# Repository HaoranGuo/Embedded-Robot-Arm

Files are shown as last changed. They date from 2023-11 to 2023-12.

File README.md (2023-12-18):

# Embedded Robot Arm
This repository is aimed for Comprehensive Training on Measurement and Control of Mechatronics Course Project at HUST.

## Overview
> In this project, the unit of length is **mm**

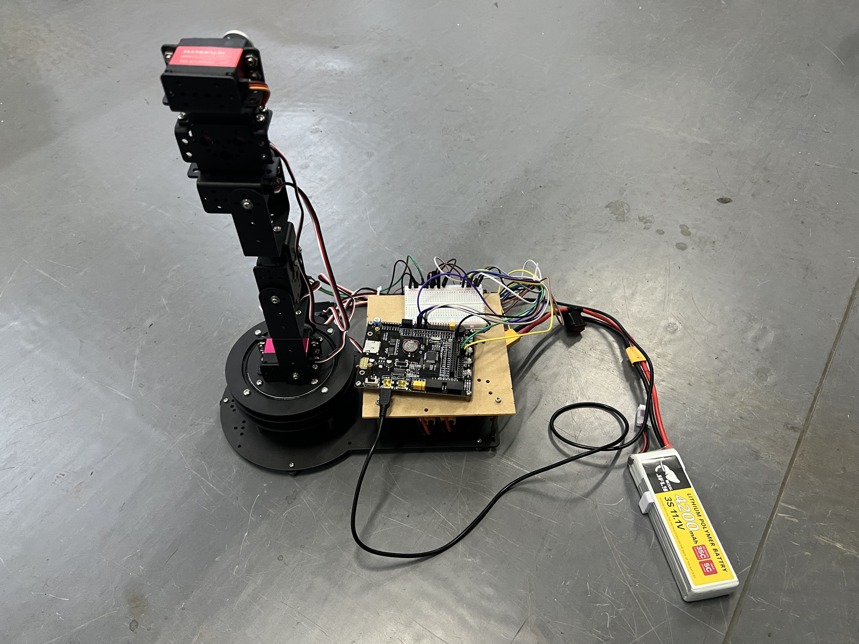
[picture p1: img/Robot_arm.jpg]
robot


In this course, we were required to start with some projects that are consist of mechanics, electrical circuits, and control systems. As a result, I decided to develop a cost-effective six-axis robotic arm.

We first refer to the key size of Universal Robot UR3. We tried to resize the robotic arm to a smaller size.

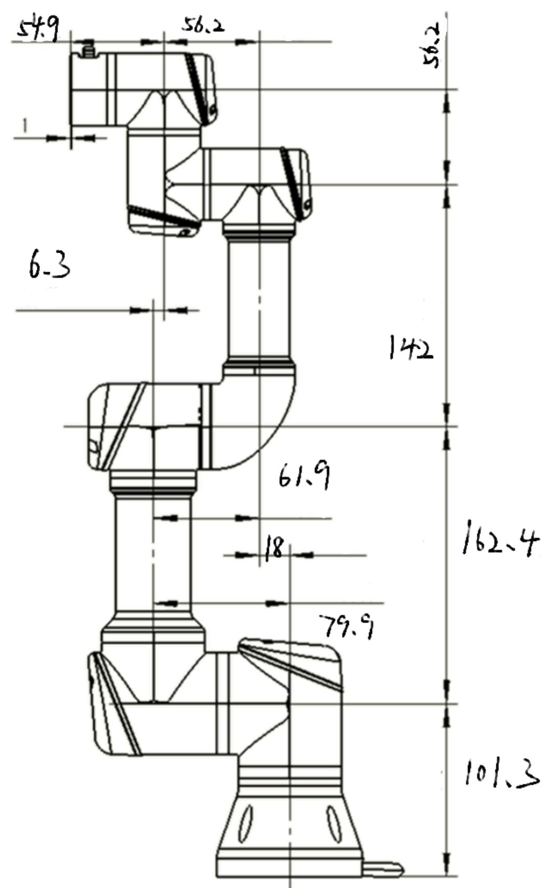
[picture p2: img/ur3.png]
ur3


This robotic arm contains six rotatable joints, allowing it to move as flexibly as possible within the workspace. The DH parameters of the robotic arm are as follows:

**Standard DH:**
| $i$ | $d_i$ | $a_i$ | $\alpha_i$ | $\theta_i$ |
| :--- | :---: | :---: | :---: | :---: |
| 1 | 0 | -9.55 | $\pi\over2$ | $\theta_1$ |
| 2 | 0 | -104 | 0 | $\theta_2$ |
| 3 | 0 | -96.4 | 0 | $\theta_3$ |
| 4 | 0 | 0 | $\pi\over2$ | $\theta_4$ |
| 5 | 80.66 | 0 | $-{{\pi}\over{2}}$ | $\theta_5$ |
| 6 | 27.5 | 0 | 0 | 0 | $\theta_6$ |

**Modified DH:**
| $i$ | $d_i$ | $a_{i-1}$ | $\alpha_{i-1}$ | $\theta_i$ |
| :--- | :---: | :---: | :---: | :---: |
| 1 | 0 | 0 | 0 | $\theta_1$ |
| 2 | 0 | -9.55 | $\pi\over2$  | $\theta_2$ |
| 3 | 0 | 104 | 0 | $\theta_3$ |
| 4 | 0 | 96.4 | 0 | $\theta_4$ |
| 5 | 80.66 | 0 | $\pi\over2$  | $\theta_5$ |
| 6 | 27.5 | 0 | $-{{\pi}\over{2}}$  | $\theta_6$ |

In this project, I used Standard DH because it can fit my robotic arm better.

## Model
Solidworks assemble model are presented in this folder. You can easily refer to the model by opening the file `Km1机械臂完整体.SLDASM` or `Km1机械臂完整体.STEP`. I built this model with `SOLIDWORDS 2022`.

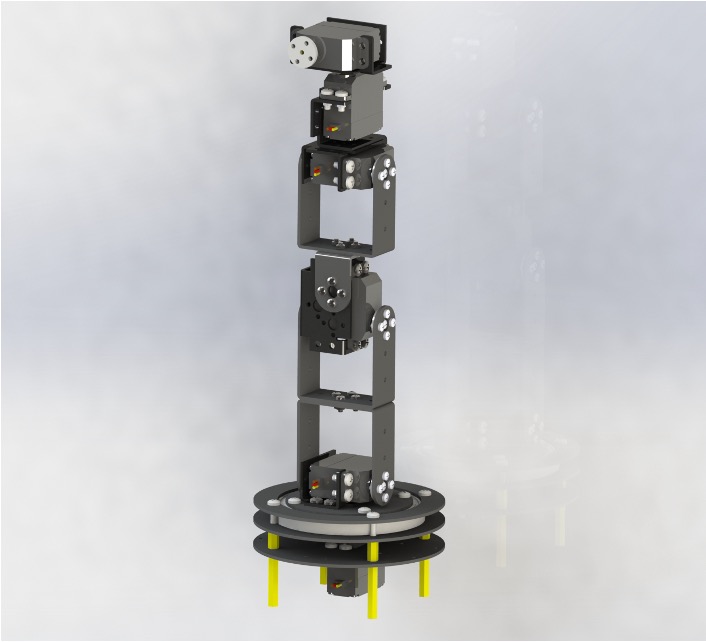
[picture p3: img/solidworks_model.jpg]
model


## Hardware
In this project, I used EmbedFire's STM32 board STM32F103 Mini. It has an **STM32F103RCT6**. The schematic of this board is shown in this folder.

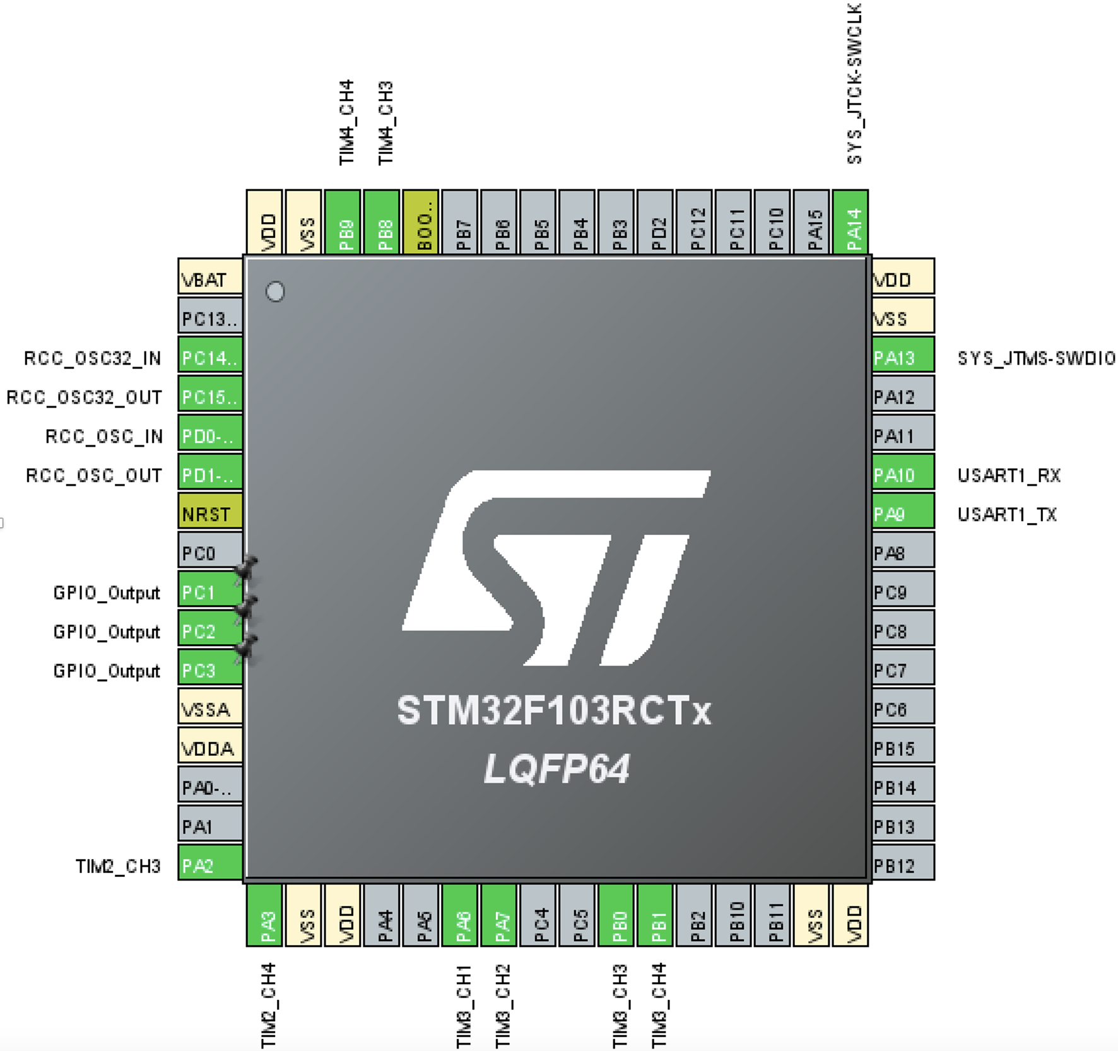
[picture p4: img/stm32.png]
stm32


In order to drive the servo, I also added some necessary module to reduce the voltage and current from the battery. 

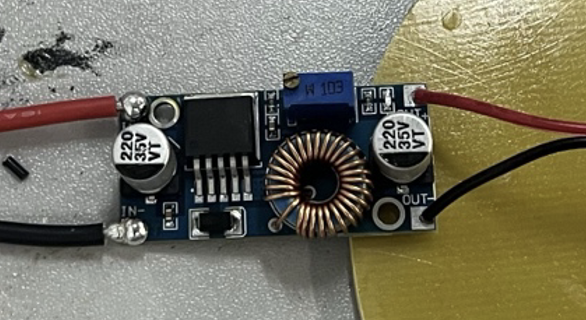
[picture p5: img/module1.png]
module1

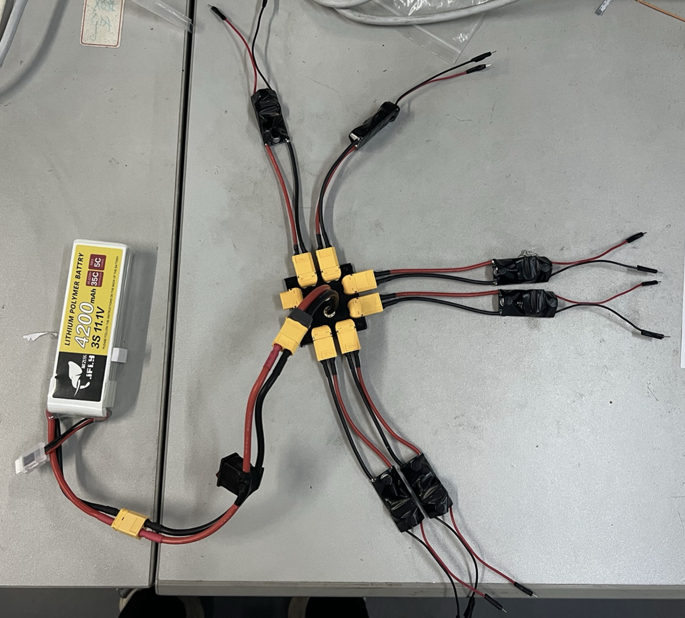
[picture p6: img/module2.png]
module2


## EmbedPrj
This code is automatically generated by `STM32CubeMX`. I also added some necessary module to communicate and drive servos.

This code is edited with `Clion`. If you want to download the code to your board, you can install `OpenOCD` and `arm-none-eabi-gcc`. Or you can choose to regenerate this code through `STM32CubeMX` to `Keil` version.

I regulated some port communication command so that people can easily debug and control it using a host computer. Some commands are as follows:

The command start with `+` and end with `,`

```+led,0,1, # open the led0```

```+ser,0,1000, # set the servo0 pulse to 1000 (1ms)```

```+servos,pulse0,pulse1,pulse2,pulse3,pulse4,pulse5, # control all the servos together```

Please note that I used a different servo at the sixth position. So the code will be a little different in this section.

![2](img/2.png)

## RobotKinetic
> This code requires `eigen`. 

This code is aimed to calculate the inverse kinetic solution. You can use it in a simple way.

1. Input the DH parameter.
2. Input the homogeneous transformation matrix or just pose `(x, y, z, rx, ry, rz)` to function `inverse_kine`.
3. Print the result.

**Please note that this code is not required. This code is only intended for validation of inverse kinematic solutions in a non-ROS environment.**

## RosPrj
> This code requires `eigen` and `ROS`.

This code is aimed to control the robotic arm. You can use it in a simple way.

- Input the DH parameter.
- Initial the seiral function.
- Use `moveJ` to move to a designated pose. You can input angle, homogeneous transformation matrix or pose `(x, y, z, rx, ry, rz)`. **Please note that I do not set a limitation in angle moving way.**
- Use `moveL` to move to a designated pose. You can input angle, homogeneous transformation matrix or pose `(x, y, z, rx, ry, rz)`. **Please note that I do not set a limitation in angle moving way.**

I also added some necessary module to communicate and drive servos and achieve some interesting applications.

- In `scripts/get_pixel.py`, I used `OpenCV` to get the pixel coordinate of the object. You can add the path manually and then drive the robot arm to the designated pose through function `draw_word`.

![daxue](img/daxue.jpg)
![robot_daxue](img/1.gif)

In the following two applications, I indeed used `ROS` Subscriber and Publisher to achieve the communication between the C++ code and Python code. 

![ROS](img/ROS.png)

- In `scripts/ros_gamepad.py`, we fulfill the function of controlling the robot arm through a simple Xbox Controller from Microsoft. Wired or wireless controllers are both supported. We recommend using a wired controller because it is more stable. Use the left joystick to control the position of x and y, and use the right joystick to control the position of z and the rotation of the end effector. Button A and Y are used to control the rotation of roll. Button B and X are used to control the rotation of pitch. Button LB and RB are used to control the rotation of yaw.

![controller](img/controller.gif)

- In `scripts/finger.py`, we fulfill the function of moving the robot arm through your finger position. We use `mediapipe` to get the position of your finger. If you try to put your thumb and index finger together, the robot arm will move to the designated pose. Plus, in order to get 3D position, we use the length of your upper middle finger in the video to calculate the distance between your finger and the camera. You can change those parameters in `scripts/finger.py`.

![finger](img/finger.gif)

## Manuscript
This PDF documents my process for deriving kinematic inverse solutions. The process references this [website](https://www.cnblogs.com/mightycode/p/9095059.html).

# Thanks
Thanks to my teammates, **Haoxiang Lian** and **Jingyuan Ma**. They helped me a lot in this project. Without them, I cannot finish this project. I feel lucky and privileged to work with them.

Thanks to my teacher, **[Prof. Lingsong He](https://mse.hust.edu.cn/info/1149/1499.htm)**, . He gave us a lot of help in this project. He also gave us a lot of advice on how to improve our robotic arm and how to improve our code.

![Haoxiang Lian](img/lhx.jpg)
![Jingyuan Ma](img/mjy.jpg)

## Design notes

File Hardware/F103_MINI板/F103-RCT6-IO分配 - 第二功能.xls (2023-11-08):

引脚序号 | 引脚名称 | 主功能（复位后） | 默认第二功能 | 可以重映射功能
1 | VBAT | VBAT
5 | OSC_IN | OSC_IN
6 | OSC_OUT | OSC_OUT
7 | NRST | NRST
60 | BOOT0 | BOOT0
12 | VSSA | VSSA
13 | VDDA | VDDA
31 | VSS_1 | VSS_1
32 | VDD_1 | VDD_1
47 | VSS_2 | VSS_2
48 | VDD_2 | VDD_2
63 | VSS_3 | VSS_3
64 | VDD_3 | VDD_3
18 | VSS_4 | VSS
19 | VDD_4 | VDD
14 | PA0-WKUP | PA0 | WKUP/USART2_CTS/ADC123_IN0/TIM2_CH1_ETR/TIM5_CH1/TIM8_ETR
15 | PA1 | PA1 | USART2_RTS/ADC123_IN1/TIM5_CH2/TIM2_CH2
16 | PA2 | PA2 | USART2_TX(8)/TIM5_CH3/ADC123_IN2/TIM2_CH3
17 | PA3 | PA3 | USART2_RX(8)/TIM5_CH4/ADC123_IN3/TIM2_CH4
20 | PA4 | PA4 | SPI1_NSS/USART2_CK/DAC_OUT1/ADC12_IN4
21 | PA5 | PA5 | SPI1_SCK/DAC_OUT2/ADC12_IN5
22 | PA6 | PA6 | SPI1_MISO/TIM8_BKIN/ADC12_IN6/TIM3_CH1 | TIM1_BKIN
23 | PA7 | PA7 | SPI1_MOSI/TIM8_CH1N/ADC12_IN7/TIM3_CH2 | TIM1_CH1N
41 | PA8 | PA8 | USART1_CK/TIM1_CH1/MCO
42 | PA9 | PA9 | USART1_TX/TIM1_CH2
43 | PA10 | PA10 | USART1_RX/TIM1_CH3
44 | PA11 | PA11 | USART1_CTS/USBDM/CAN_RX/TIM1_CH4
45 | PA12 | PA12 | USART1_RTS/USBDP/CAN_TX/TIM1_ETR
46 | PA13 | JTMSSWDIO |  | PA13
49 | PA14 | JTCKSWCLK |  | PA14
50 | PA15 | JTDI | SPI3_NSS/I2S3_WS | TIM2_CH1_ETR/PA15/SPI1_NSS
26 | PB0 | PB0 | ADC12_IN8/TIM3_CH3/TIM8_CH2N | TIM1_CH2N
27 | PB1 | PB1 | ADC12_IN9/TIM3_CH4/TIM8_CH3N | TIM1_CH3N
28 | PB2 | PB2/BOOT1
55 | PB3 | JTDO | SPI3_SCK/I2S3_CK | PB3/TRACESWO/TIM2_CH2/SPI1_SCK
56 | PB4 | NJTRST | SPI3_MISO | PB4/TIM3_CH1/SPI1_MISO
57 | PB5 | PB5 | I2C1_SMBA/SPI3_MOSI/I2S3_SD | TIM3_CH2/SPI1_MOSI
58 | PB6 | PB6 | I2C1_SCL/TIM4_CH1 | USART1_TX
59 | PB7 | PB7 | I2C1_SDA/FSMC_NADV/TIM4_CH2 | USART1_RX
61 | PB8 | PB8 | TIM4_CH3/SDIO_D4 | I2C1_SCL/CAN_RX
62 | PB9 | PB9 | TIM4_CH4/SDIO_D5 | I2C1_SDA/CAN_TX
29 | PB10 | PB10 | I2C2_SCL/USART3_TX | TIM2_CH3
30 | PB11 | PB11 | I2C2_SDA/USART3_RX | TIM2_CH4
33 | PB12 | PB12 | SPI2_NSS/I2S2_WS/I2C2_SMBA/USART3_CK/TIM1_BKIN
34 | PB13 | PB13 | SPI2_SCK/I2S2_CK/USART3_CTS/TIM1_CH1N
35 | PB14 | PB14 | SPI2_MISO/TIM1_CH2N/USART3_RTS
36 | PB15 | PB15 | SPI2_MOSI/I2S2_SD/TIM1_CH3N
8 | PC0 | PC0 | ADC123_IN10
9 | PC1 | PC1 | ADC123_IN11
10 | PC2 | PC2 | ADC123_IN12
11 | PC3 | PC3 | ADC123_IN13
24 | PC4 | PC4 | ADC12_IN14
25 | PC5 | PC5 | ADC12_IN15
37 | PC6 | PC6 | I2S2_MCK/TIM8_CH1/SDIO_D6 | TIM3_CH1
38 | PC7 | PC7 | I2S3_MCK/TIM8_CH2/SDIO_D7 | TIM3_CH2
39 | PC8 | PC8 | TIM8_CH3/SDIO_D0 | TIM3_CH3
40 | PC9 | PC9 | TIM8_CH4/SDIO_D1 | TIM3_CH4
51 | PC10 | PC10 | UART4_TX/SDIO_D2 | USART3_TX
52 | PC11 | PC11 | UART4_RX/SDIO_D3 | USART3_RX
53 | PC12 | PC12 | UART5_TX/SDIO_CK | USART3_CK
2 | PC13-TAMPERRTC | PC13 | TAMPER-RTC
3 | PC14-OSC32_IN | PC14 | OSC32_IN
4 | PC15-OSC32_OUT | PC15 | OSC32_OUT
54 | PD2 | PD2 | TIM3_ETR/UART5_RX/SDIO_CMD

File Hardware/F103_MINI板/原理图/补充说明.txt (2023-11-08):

目前部分板子上装的是内置晶振的CH340C，它与需要外置晶振的CH340G功能一致。
若是发现底板的USB转串口旁边的焊盘没有晶振，不是因为少焊了晶振，而是晶振已经内置到CH340内部了。

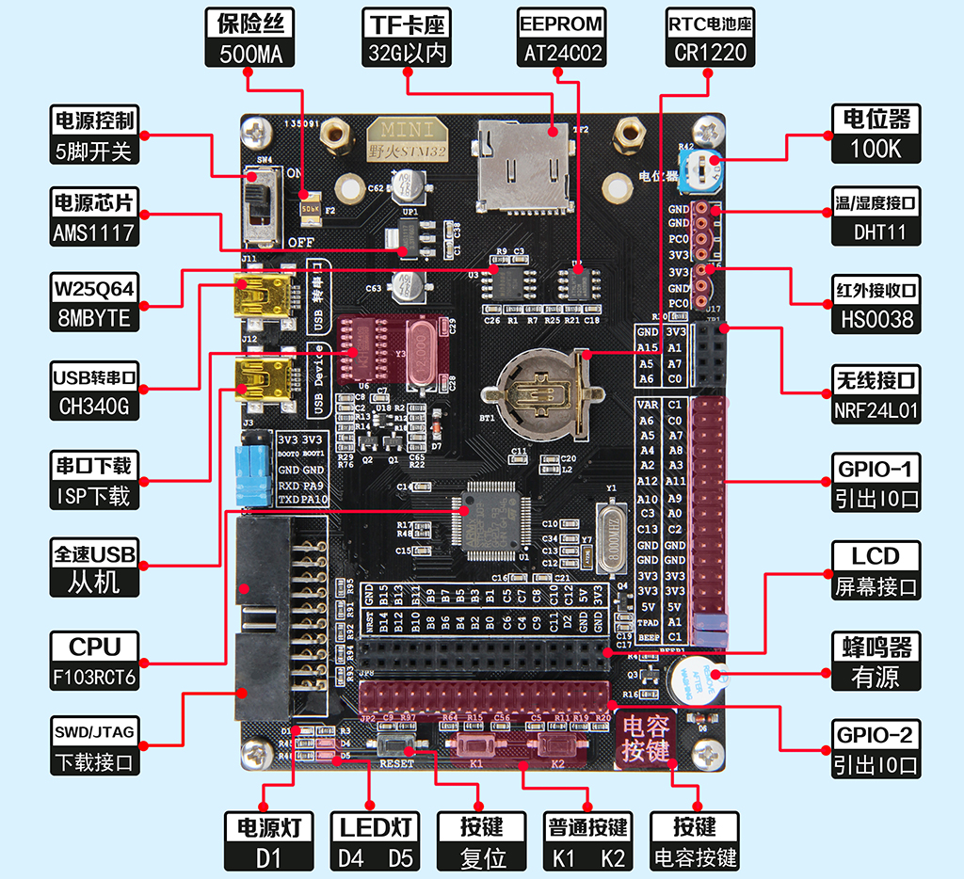
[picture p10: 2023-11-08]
Hardware/F103_MINI板/F103-MINI硬件资源描述图.jpg

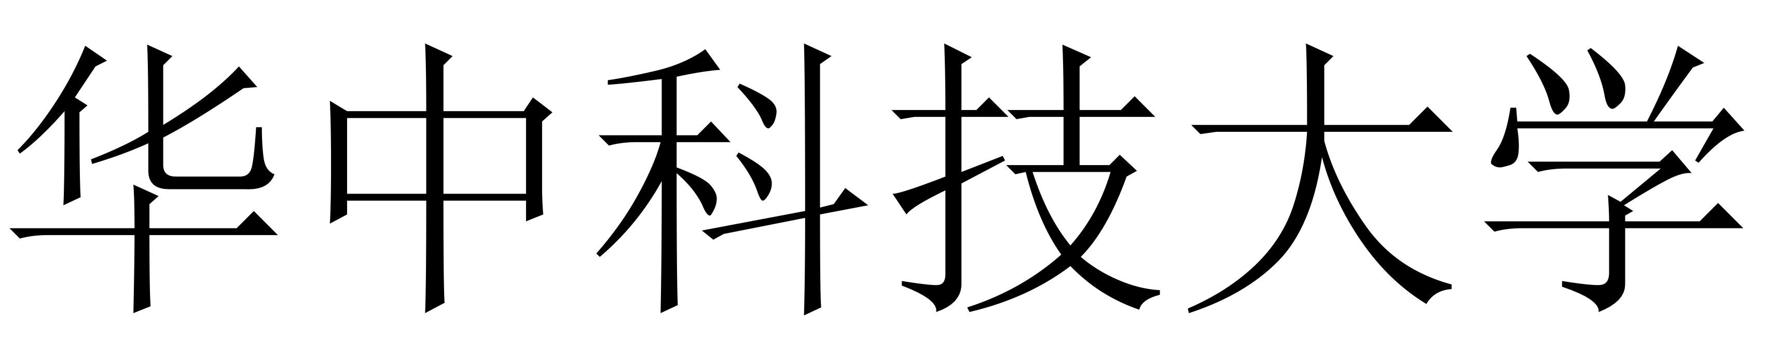
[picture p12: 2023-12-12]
RosPrj/img/hust.png

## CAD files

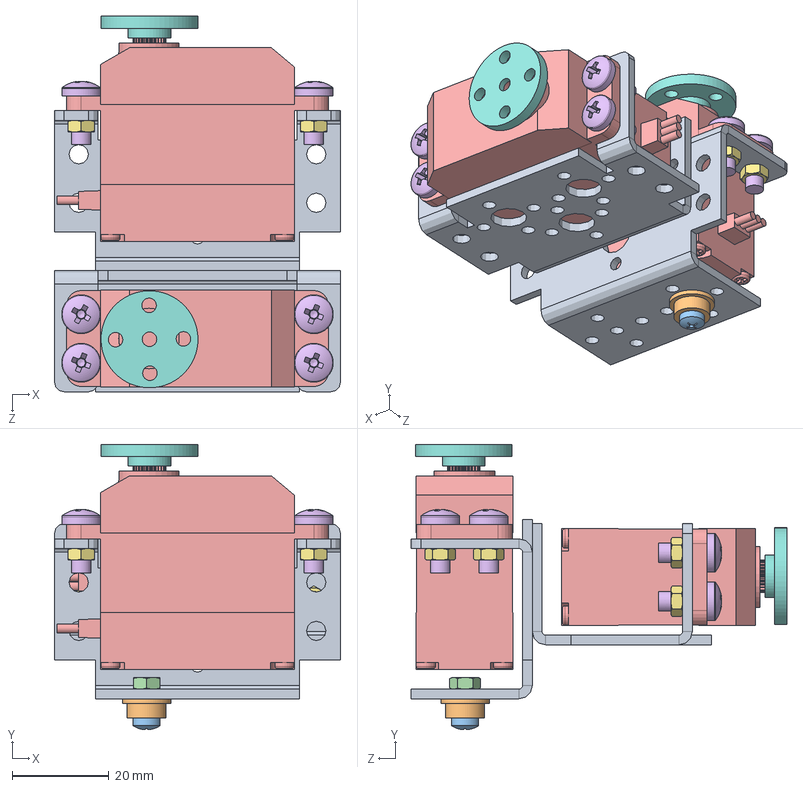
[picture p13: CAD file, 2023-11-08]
Model/支架组合体.SLDASM
59.0 x 58.9 x 77.5 mm
JXS006 x 2
杯式轴承
GB818-M3X8-ZN-4.8
GB6170-M3-ZN-10
单轴舵机 x 2
GB818-M4X10-4.8 x 8
GB6170-M4-ZN-10 x 8
金属主舵盘 x 2

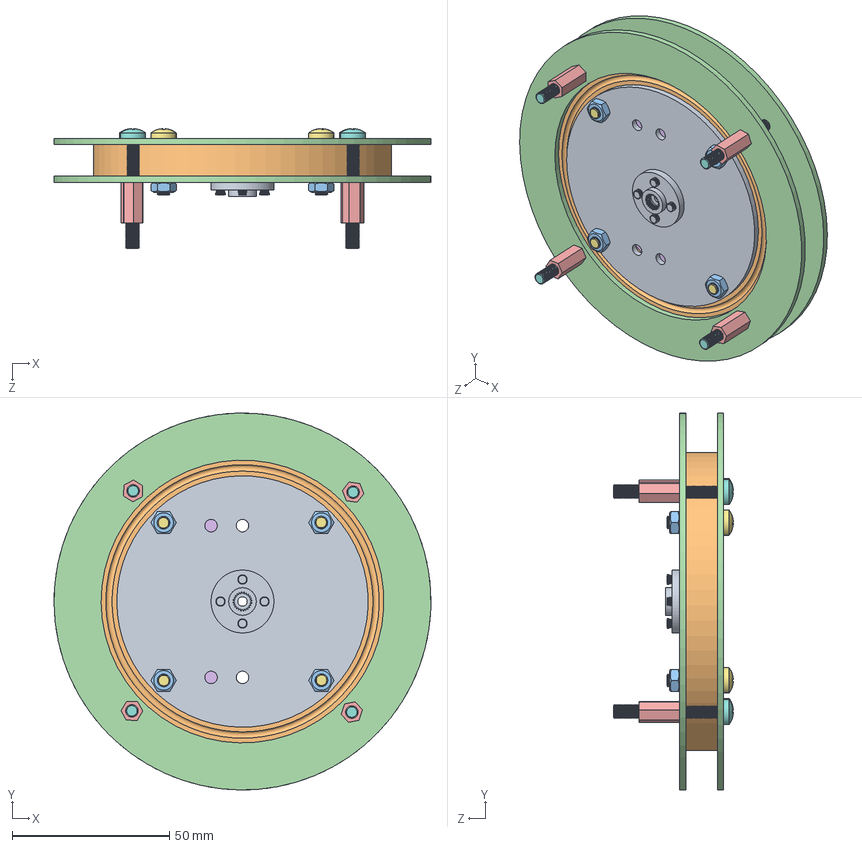
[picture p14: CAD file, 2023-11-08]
Model/一自由度云台.SLDASM
120.0 x 120.0 x 38.1 mm
001小圆盘+舵盘Z
大轴承
hex nuts, style 1-grades ab gb x 4
圆环 x 2
M4X13双通铜柱 x 4
小圆盘
螺丝M4X18 x 4
螺丝M4X35 x 4

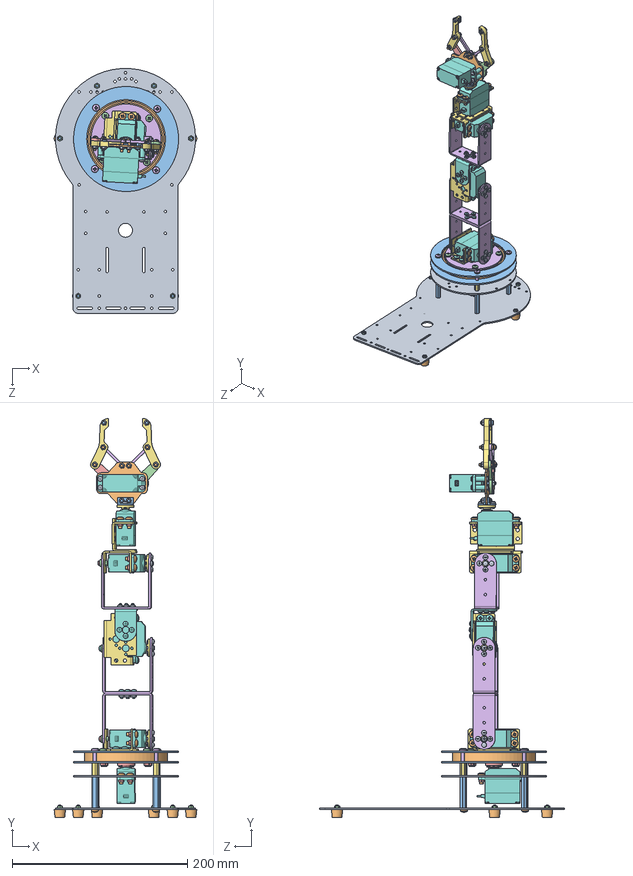
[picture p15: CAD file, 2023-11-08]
Model/Km1机械臂完整体.SLDASM
163.0 x 455.9 x 279.8 mm
大底板
jiaodian x 6
GB818-M3X10-ZN-4.8 x 10
GB6170-M3-ZN-10 x 8
001小圆盘+舵盘Z
小圆盘
JXS006 x 4
cross recessed pan head screws gb x 21
hex nuts, style 1-grades ab gb x 20
大轴承
圆环 x 2
GB818-M4X18 x 4
GB6170-M4-ZN-10 x 20
GB818-M4X35 x 4
M4X14双通铜柱 x 4
单轴舵机 x 6
舵机圆盘
GB818-M4X10-4.8 x 20
M4X35双通铜柱 x 4
杯式轴承 x 3
GB818-M3X8-ZN-4.8 x 2
JXS005 x 3
金属主舵盘 x 5
JXS007
GB818-M3X6-ZN-4.8 x 27
手爪 （新）
安装扣 x 2
爪子齿轮 2
爪子齿轮
小横杆 x 2
长杆 x 2
螺柱 x 4
GB6170-M3（自锁） x 11
GB818-M3X14-ZN-4.8 x 6
GB818-M3X12-ZN-4.8

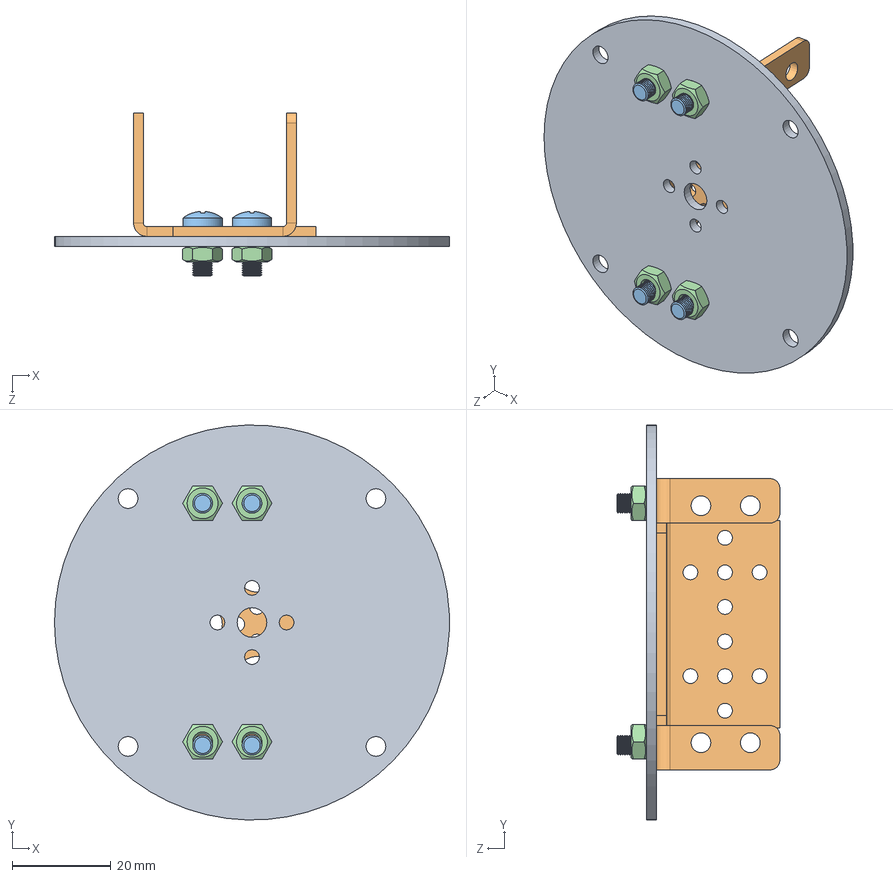
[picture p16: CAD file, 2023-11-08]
Model/002小圆盘+支架.SLDASM
80.0 x 80.0 x 33.0 mm
小圆盘
JXS006
cross recessed pan head screws gb x 4
hex nuts, style 1-grades ab gb x 4

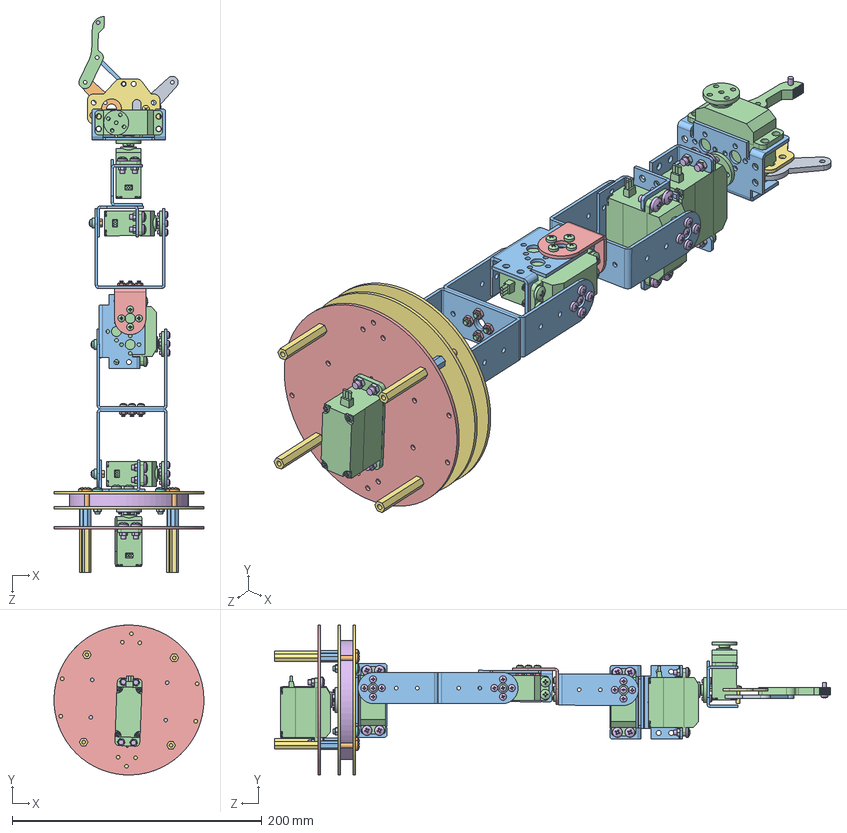
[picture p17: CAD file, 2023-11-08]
Model/6自由度机械臂完美.SLDASM
120.0 x 120.0 x 444.9 mm
001小圆盘+舵盘Z
小圆盘
JXS006 x 5
cross recessed pan head screws gb x 21
hex nuts, style 1-grades ab gb x 20
大轴承
圆环 x 2
GB818-M4X18 x 4
GB6170-M4-ZN-10 x 20
GB818-M4X35 x 4
M4X14双通铜柱 x 4
单轴舵机 x 6
舵机圆盘
GB818-M4X10-4.8 x 16
M4X35双通铜柱 x 4
杯式轴承 x 3
GB818-M3X8-ZN-4.8 x 2
GB6170-M3-ZN-10 x 2
JXS005 x 3
金属主舵盘 x 5
JXS007
GB818-M3X6-ZN-4.8 x 18

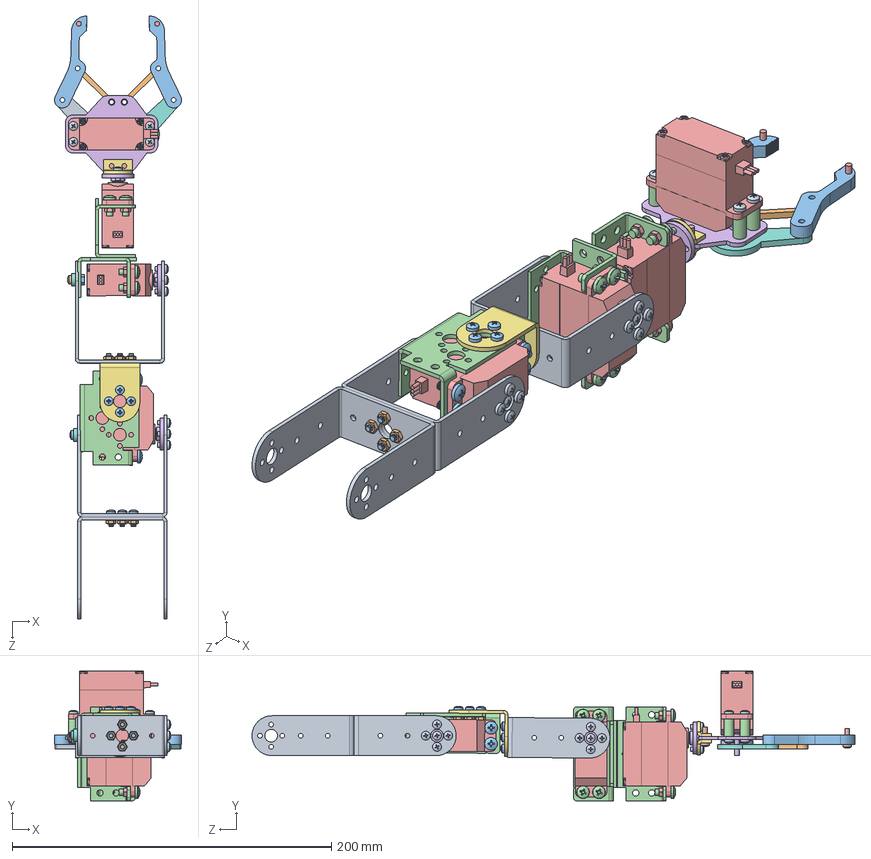
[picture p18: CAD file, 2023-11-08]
Model/机械臂体含爪子.SLDASM
79.7 x 81.4 x 378.0 mm
JXS005 x 3
hex nuts, style 1-grades ab gb x 16
cross recessed pan head screws gb x 17
JXS006 x 3
单轴舵机 x 4
金属主舵盘 x 4
JXS007
杯式轴承 x 2
GB818-M3X6-ZN-4.8 x 22
GB818-M3X8-ZN-4.8
GB6170-M3-ZN-10
GB818-M4X10-4.8 x 8
GB6170-M4-ZN-10 x 8
手爪 （新）
安装扣 x 2
爪子齿轮 2
爪子齿轮
小横杆 x 2
长杆 x 2
螺柱 x 4
GB818-M3X10-ZN-4.8 x 4
GB818-M3X12-ZN-4.8

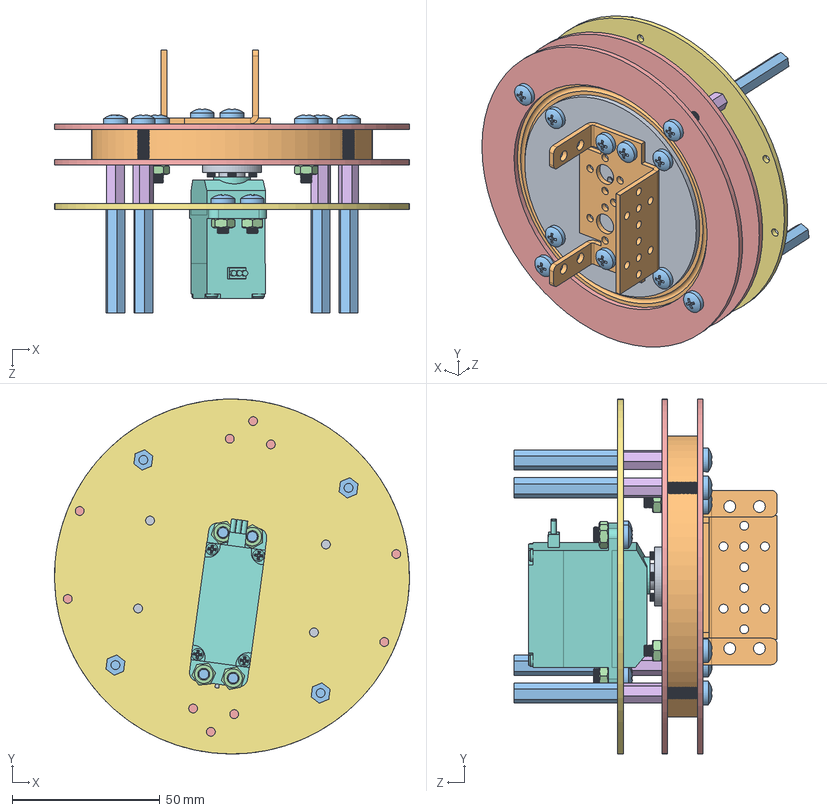
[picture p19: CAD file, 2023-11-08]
Model/云台综合体.SLDASM
120.0 x 120.0 x 89.0 mm
001小圆盘+舵盘Z
大轴承
cross recessed pan head screws gb x 16
hex nuts, style 1-grades ab gb x 12
圆环 x 2
M4X13双通铜柱 x 4
舵机圆盘
单轴舵机
小圆盘
JXS006
M4X35双通铜柱 x 4

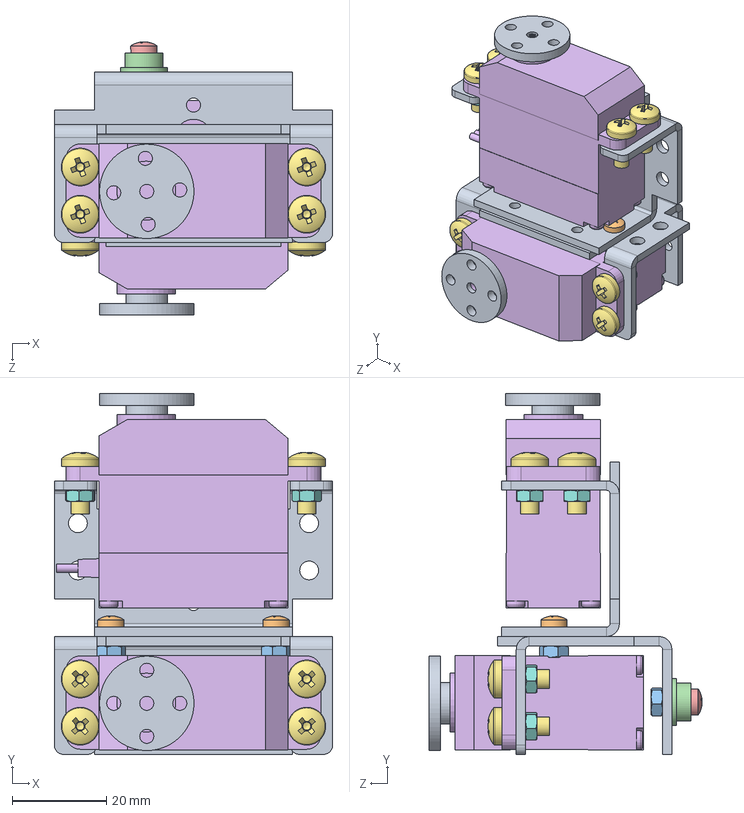
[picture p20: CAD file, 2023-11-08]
Model/008 舵机支架组合.SLDASM
59.0 x 76.5 x 57.9 mm
多功能支架 x 2
GB818-M3X6-ZN-4.8 x 2
GB6170-M3-ZN-10 x 3
杯式轴承
GB818-M3X8-ZN-4.8
单轴舵机 x 2
GB818-M4X10-4.8 x 8
GB6170-M4-ZN-10 x 8
金属主舵盘 x 2

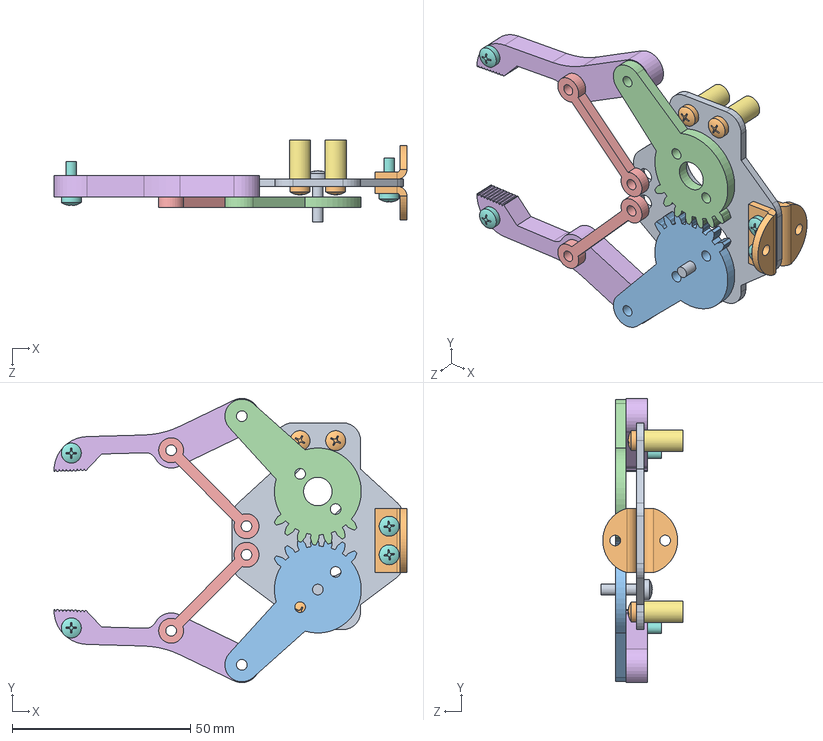
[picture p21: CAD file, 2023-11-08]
Model/爪子（配合）.SLDASM
99.0 x 79.7 x 23.0 mm
手爪 （新）
安装扣 x 2
爪子齿轮 2
爪子齿轮
小横杆 x 2
长杆 x 2
螺柱 x 4
GB818-M3X10-ZN-4.8 x 4
GB818-M3X12-ZN-4.8
GB818-M3X6-ZN-4.8 x 4

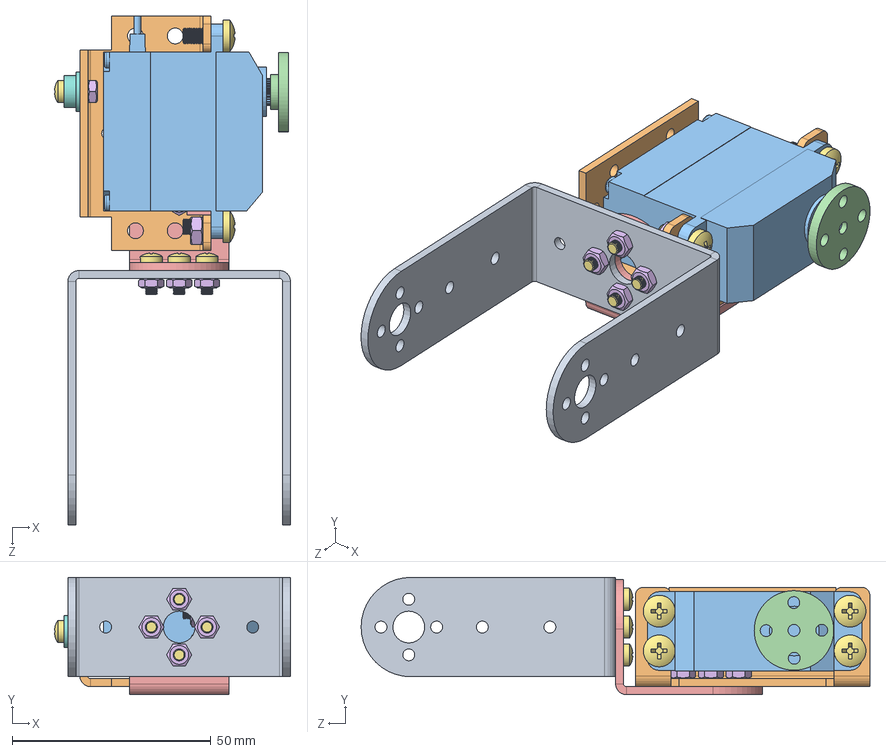
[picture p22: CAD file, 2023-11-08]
Model/007 长U支架组合.SLDASM
59.4 x 29.5 x 128.0 mm
JXS005
JXS006
单轴舵机
金属主舵盘
JXS007
hex nuts, style 1-grades ab gb x 11
cross recessed pan head screws gb x 9
杯式轴承

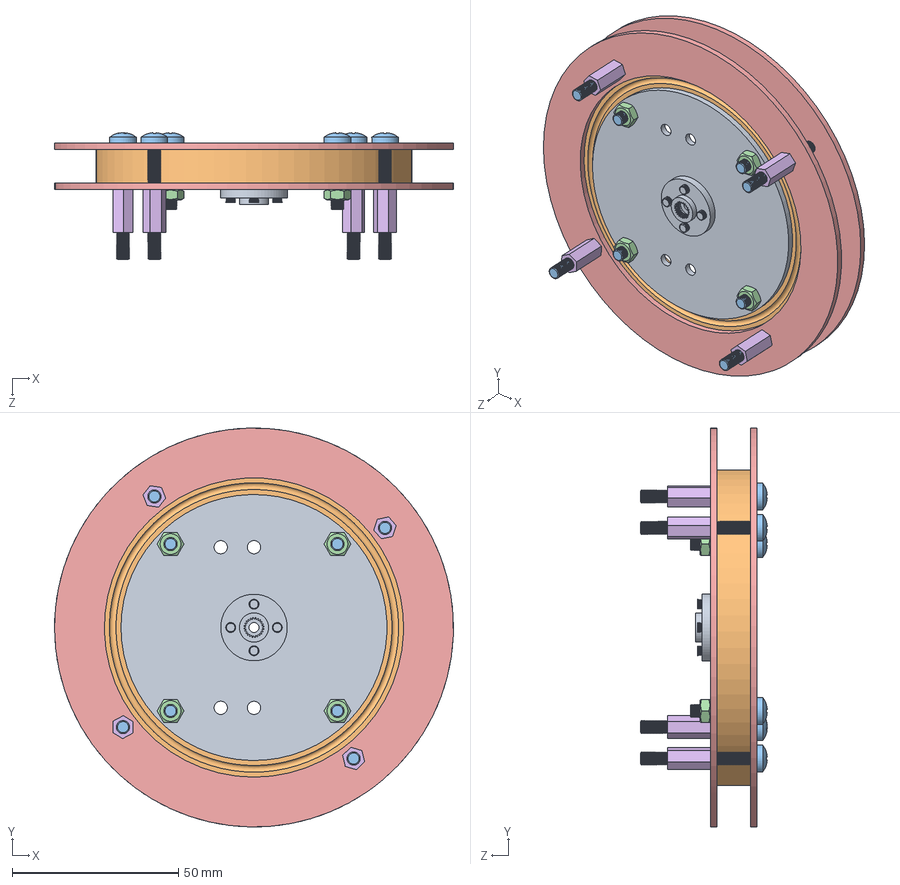
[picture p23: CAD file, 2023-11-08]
Model/003 云台.SLDASM
120.0 x 120.0 x 38.1 mm
001小圆盘+舵盘Z
大轴承
cross recessed pan head screws gb x 8
hex nuts, style 1-grades ab gb x 4
圆环 x 2
M4X13双通铜柱 x 4

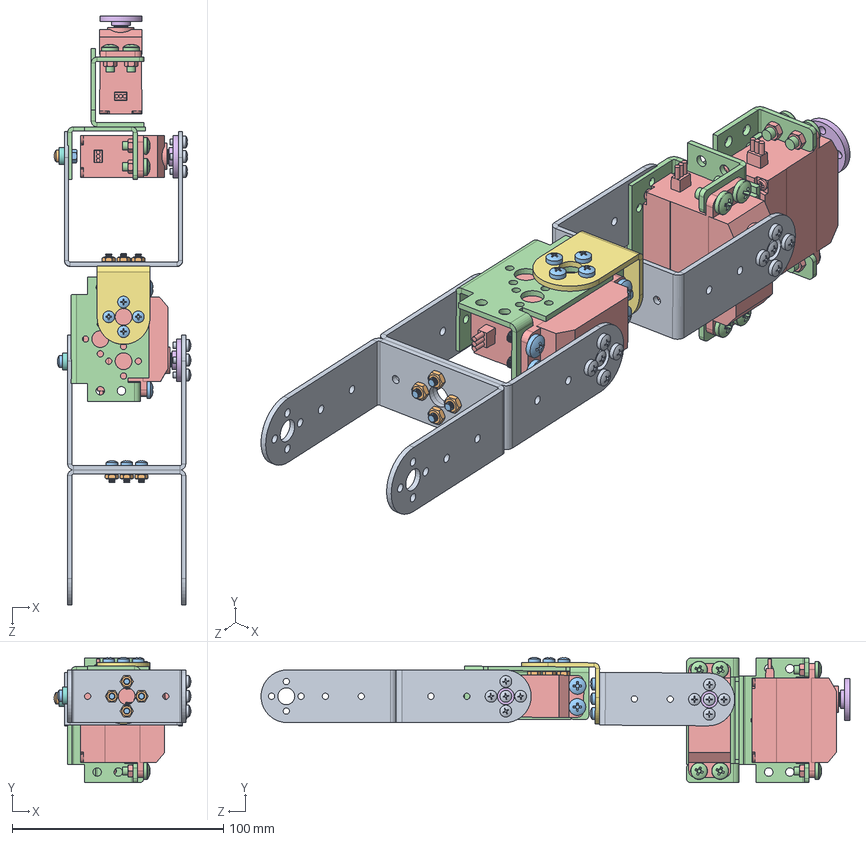
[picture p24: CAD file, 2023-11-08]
Model/机械臂体.SLDASM
64.8 x 59.3 x 279.0 mm
JXS005 x 3
hex nuts, style 1-grades ab gb x 16
cross recessed pan head screws gb x 17
JXS006 x 3
单轴舵机 x 3
金属主舵盘 x 3
JXS007
杯式轴承 x 2
GB818-M3X6-ZN-4.8 x 10
GB818-M3X8-ZN-4.8
GB6170-M3-ZN-10
GB818-M4X10-4.8 x 8
GB6170-M4-ZN-10 x 8

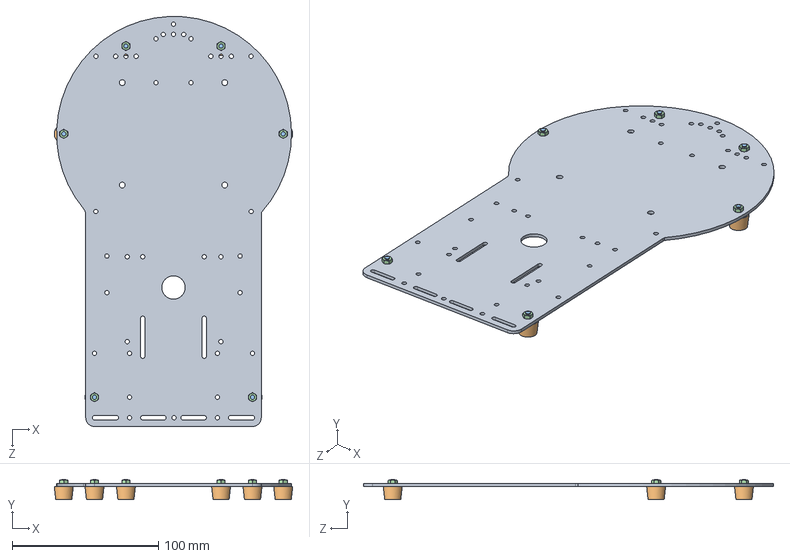
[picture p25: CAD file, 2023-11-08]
Model/Km1底板.SLDASM
163.0 x 14.0 x 280.2 mm
大底板
jiaodian x 6
GB818-M3X10-ZN-4.8 x 6
GB6170-M3-ZN-10 x 6

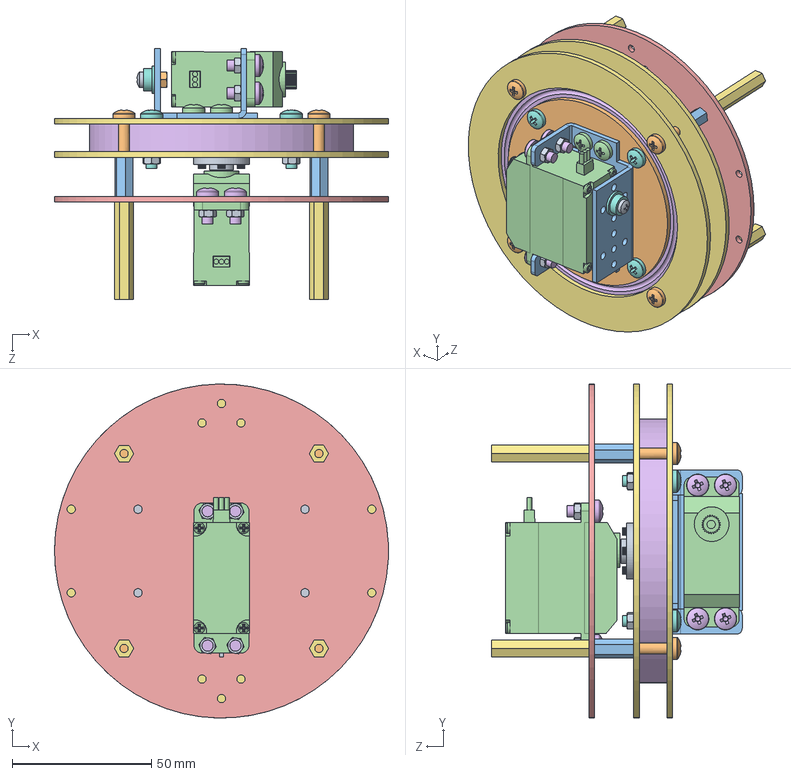
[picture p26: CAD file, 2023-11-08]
Model/2自由度云台完美.SLDASM
120.0 x 120.0 x 90.0 mm
001小圆盘+舵盘Z
小圆盘
JXS006
cross recessed pan head screws gb x 4
hex nuts, style 1-grades ab gb x 4
大轴承
圆环 x 2
GB818-M4X18 x 4
GB6170-M4-ZN-10 x 12
GB818-M4X35 x 4
M4X14双通铜柱 x 4
单轴舵机 x 2
舵机圆盘
GB818-M4X10-4.8 x 8
M4X35双通铜柱 x 4
杯式轴承
GB818-M3X8-ZN-4.8
GB6170-M3-ZN-10

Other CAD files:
Model/云台综合整体.SLDASM
Model/006 长U组合.SLDASM
Model/004 圆盘舵机.SLDASM
Model/长u连接件连接中间件.SLDASM
Model/001小圆盘+舵盘Z.SLDPRT
Model/GB6170-M3-ZN-10.SLDPRT
Model/GB6170-M4-ZN-10.SLDPRT
Model/GB818-M3X10-ZN-4.8.SLDPRT
Model/GB818-M3X12-ZN-4.8.SLDPRT
Model/GB818-M3X6-ZN-4.8.SLDPRT
Model/GB818-M3X8-ZN-4.8.SLDPRT
Model/GB818-M4X10-4.8.SLDPRT
Model/GB818-M4X18.SLDPRT
Model/GB818-M4X35.SLDPRT
Model/JXS005.SLDPRT
Model/JXS006.SLDPRT
Model/JXS007.SLDPRT
Model/M4X14双通铜柱.SLDPRT
Model/M4X35双通铜柱.SLDPRT
Model/jiaodian.SLDPRT
Model/单轴舵机.SLDPRT
Model/圆环.SLDPRT
Model/垫片.SLDPRT
Model/大底板.SLDPRT
Model/大轴承.SLDPRT
Model/安装扣.SLDPRT
Model/小圆盘.SLDPRT
Model/小横杆.SLDPRT
Model/手爪 （新）.SLDPRT
Model/杯式轴承.SLDPRT
Model/爪子齿轮 2.SLDPRT
Model/爪子齿轮.SLDPRT
Model/舵机圆盘.SLDPRT
Model/螺柱.SLDPRT
Model/金属主舵盘.SLDPRT
Model/长U支架.SLDPRT
Model/长杆.SLDPRT

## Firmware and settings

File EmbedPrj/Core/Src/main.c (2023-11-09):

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
/* Includes ------------------------------------------------------------------*/
#include "main.h"
#include "tim.h"
#include "usart.h"
#include "gpio.h"


void SystemClock_Config(void);
/* USER CODE BEGIN 0 */

void user_Function(uint8_t* string){
    uint8_t* pt = string + 1;
    uint8_t num = 0;
    while(*string != '+'){
        string++;
        pt = string + 1;
        num++;
    }
    if ((*pt == 'L' || *pt == 'l') &&
        (*(pt+1) == 'E' || *(pt+1) == 'e') &&
        (*(pt+2) == 'D' || *(pt+2) == 'd') &&
        (*(pt+3) == ',')) {
        pt = pt + 4;
        uint8_t idx;
        uint8_t led_num = 0;
        for (idx = 0; *(pt + idx) != ','; idx++) {
            led_num *= 10;
            led_num += *(pt + idx) - '0';
        }
        pt = pt + idx + 1;
        uint8_t led_sta = 0;
        for (idx = 0; *(pt + idx) != ','; idx++) {
            led_sta *= 10;
            led_sta += *(pt + idx) - '0';
        }
        if (led_num == 0) {
            if (led_sta == 0) {
                LED0_OFF();
                uint8_t TX_Str[] = "\r\nLED0: Close\r\n";
                HAL_UART_Transmit(&huart1, TX_Str, sizeof(TX_Str), 1000);
            } else if (led_sta == 1) {
                LED0_ON();
                uint8_t TX_Str[] = "\r\nLED0: Open\r\n";
                HAL_UART_Transmit(&huart1, TX_Str, sizeof(TX_Str), 1000);
            } else {
                uint8_t TX_Str[] = "\r\nLED0: Status Error\r\n";
                HAL_UART_Transmit(&huart1, TX_Str, sizeof(TX_Str), 1000);
            }
        } else if (led_num == 1) {
            if (led_sta == 0) {
                LED1_OFF();
                uint8_t TX_Str[] = "\r\nLED1: Close\r\n";
                HAL_UART_Transmit(&huart1, TX_Str, sizeof(TX_Str), 1000);
            } else if (led_sta == 1) {
                LED1_ON();
                uint8_t TX_Str[] = "\r\nLED1: Open\r\n";
                HAL_UART_Transmit(&huart1, TX_Str, sizeof(TX_Str), 1000);
            } else {
                uint8_t TX_Str[] = "\r\nLED1: Status Error\r\n";
                HAL_UART_Transmit(&huart1, TX_Str, sizeof(TX_Str), 1000);
            }
        } else {
            uint8_t TX_Str[] = "\r\nLED: Index Error\r\n";
            HAL_UART_Transmit(&huart1, TX_Str, sizeof(TX_Str), 1000);
        }
    }
    else if ((*pt == 'S' || *pt == 's') &&
             (*(pt+1) == 'E' || *(pt+1) == 'e') &&
             (*(pt+2) == 'R' || *(pt+2) == 'r') &&
             (*(pt+3) == ',')) {
        pt = pt + 4;
        uint8_t idx;
        uint8_t servo_num = 0;
        for (idx = 0; *(pt+idx)!= ','; idx++){
            servo_num *= 10;
            servo_num += *(pt+idx) - '0';
        }
        pt = pt + idx + 1;
        if (servo_num < 0 || servo_num > USED_SERVO_NUM){
            uint8_t TX_Str[] = "\r\nSERVO: Index Error\r\n";
            HAL_UART_Transmit(&huart1, TX_Str, sizeof(TX_Str), 1000);
        }
        else{
            uint16_t servo_pulse_t = 0;
            for (idx = 0; *(pt + idx) != ','; idx++) {
                servo_pulse_t *= 10;
                servo_pulse_t = servo_pulse_t + (uint16_t)(*(pt + idx) - '0');
            }

            servo_Move(servo_num, servo_pulse_t);

            uint8_t TX_Str[] = "\r\nSER: Move Successfully\r\n";
            HAL_UART_Transmit(&huart1, TX_Str, sizeof(TX_Str), 1000);
        }
    }
    else if ((*pt == 'S' || *pt == 's') &&
             (*(pt+1) == 'E' || *(pt+1) == 'e') &&
             (*(pt+2) == 'R' || *(pt+2) == 'r') &&
             (*(pt+3) == 'V' || *(pt+3) == 'v') &&
             (*(pt+4) == 'O' || *(pt+4) == 'o') &&
             (*(pt+5) == 'S' || *(pt+5) == 's') &&
             (*(pt+6) == ',')) {
        pt = pt + 7;
        uint8_t idx;
        uint8_t valid = 0;
        uint16_t angle_pulse[USED_SERVO_NUM] = {0};
        for(uint8_t i = 0; i < USED_SERVO_NUM; ++i){
            uint8_t flag = 0;
            for (idx = 0; *(pt + idx) != ','; idx++) {
                angle_pulse[i] *= 10;
                angle_pulse[i] = angle_pulse[i] + (uint16_t)(*(pt + idx) - '0');
            }
            if (angle_pulse[i] < 500 || angle_pulse[i] > 2500){
                valid = 1;
                break;
            }
            pt = pt + idx + 1;
            servo_pulse_last[i] = servo_pulse[i];
            servo_pulse[i] = angle_pulse[i];
        }
        if (valid == 0){
            uint8_t TX_Str[] = "\r\nSERVOS: Move Successfully\r\n";
            HAL_UART_Transmit(&huart1, TX_Str, sizeof(TX_Str), 1000);

            servo_Move2Goal();
        }
        else{
            uint8_t TX_Str[] = "\r\nSERVOS: Angle Setting Error\r\n";
            HAL_UART_Transmit(&huart1, TX_Str, sizeof(TX_Str), 1000);
        }
    }
    else{
        uint8_t TX_Str[] = "\r\nUnknown Command\r\n";
        HAL_UART_Transmit(&huart1, TX_Str, sizeof(TX_Str), 1000);
    }
}

/* USER CODE END 0 */

/**
  * @brief  The application entry point.
  * @retval int
  */
int main(void)
{
  /* MCU Configuration--------------------------------------------------------*/

  /* Reset of all peripherals, Initializes the Flash interface and the Systick. */
  HAL_Init();

  /* Configure the system clock */
  SystemClock_Config();

  /* Initialize all configured peripherals */
  MX_GPIO_Init();
  MX_TIM2_Init();
  MX_TIM3_Init();
  MX_TIM4_Init();
  MX_USART1_UART_Init();
  /* USER CODE BEGIN 2 */

    BEEP_ON();
    servo_Init();
    BEEP_OFF();

    uint8_t TX_Str1[] = "\r\nInit Successfully\r\n";
    uint8_t TX_Str2[] = "\r\nType: \"+FUNCTION,PARAMETER1,PARAMETER2,...\" to command the board. E.g.\"+LED,1,1,\" can open the LED1.\r\n";
    HAL_UART_Transmit(&huart1, TX_Str1, sizeof(TX_Str1), 1000);
    HAL_UART_Transmit(&huart1, TX_Str2, sizeof(TX_Str2), 1000);

    HAL_UART_Receive_IT(&huart1, (uint8_t *)rx_buffer, RXBUFFERSIZE);

  /* USER CODE END 2 */

  /* Infinite loop */
  /* USER CODE BEGIN WHILE */
  while (1)
  {
    /* USER CODE END WHILE */

    /* USER CODE BEGIN 3 */

      if (usart_rx_sta & 0x8000){
          user_Function(usart_rx_buf);
          usart_rx_sta = 0;
      }
      else {
          HAL_Delay(10);
      }

  }
  /* USER CODE END 3 */
}

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


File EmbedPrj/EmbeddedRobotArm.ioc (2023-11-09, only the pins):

Mcu.UserName=STM32F103RCTx
PA10.Signal=USART1_RX
PA13.Signal=SYS_JTMS-SWDIO
PA14.Signal=SYS_JTCK-SWCLK
PA2.Signal=S_TIM2_CH3
PA3.Signal=S_TIM2_CH4
PA6.Signal=S_TIM3_CH1
PA7.Signal=S_TIM3_CH2
PA9.Signal=USART1_TX
PB0.Signal=S_TIM3_CH3
PB1.Signal=S_TIM3_CH4
PB8.Signal=S_TIM4_CH3
PB9.Signal=S_TIM4_CH4
PC1.Signal=GPIO_Output
PC14-OSC32_IN.Signal=RCC_OSC32_IN
PC15-OSC32_OUT.Signal=RCC_OSC32_OUT
PC2.Signal=GPIO_Output
PC3.Signal=GPIO_Output
PD0-OSC_IN.Signal=RCC_OSC_IN
PD1-OSC_OUT.Signal=RCC_OSC_OUT

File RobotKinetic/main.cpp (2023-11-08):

#include "kinetic.h"
#include <iostream>
#include <vector>
#include <Eigen/Dense>

int main(int argc, char** argv){

    /*
    改进DH表    a(i-1)     alpha(i-1)    di
    Arm1  =   [0,          0,        80  ];
    Arm2  =   [-9.55,      pi/2,    0  ];
    Arm3  =   [104,        0,        0  ];
    Arm4  =   [96.4,       0,        0  ];
    Arm5  =   [0,          pi/2,     80.66];
    Arm6  =   [0,          -pi/2,     27.5 ];
    */

    /*
    这里用的应该是标准DH表来计算机器人，参考UR3的标准DH进行修改
    标准DH表    d(i)    a(i)    alpha(i)
    1           0       -9.55    PI/2
    2           0       -104    0
    3           0       -96.4   0
    4           0       0       PI/2
    5           80.66   0       -PI/2
    6           27.5    0       0
    */
    std::vector<double> a = {-9.55, -104, -96.4, 0, 0, 0};
    std::vector<double> d = {0, 0, 0, 0, 80.66, 27.5};
    std::vector<double> alpha = {PI/2, 0, 0, PI/2, -PI/2, 0};

//    std::vector<double> a = {0, -425, -392, 0, 0, 0};
//    std::vector<double> d = {89.2, 0, 0, 109.3, 94.75, 82.5};
//    std::vector<double> alpha = {PI/2, 0, 0, PI/2, -PI/2, 0};

    Kinetic ur3(a, d, alpha);

    // ur3.printDH();

    Eigen::Matrix4d T;
//     T << 1, 0, 0, 50,
//          0, 1, 0, 40,
//          0, 0, 1, 50,
//          0, 0, 0, 1;
    T = ur3.pose2T(180, 40, 50, PI/4, -PI/6, PI/5);
    //T = ur3.pose2T(50, 30, 50, 0, 0, 0);

    ur3.setT(T);
    ur3.printT();

    std::vector<std::vector<double>> result;
    ur3.inverse_kine(result);
    ur3.get_possible_angle();
    ur3.printResult();
    ur3.printPossibleResult();

    Eigen::Matrix4d res;

    for (int i = 0; i < ur3._result.size(); ++i){
        if (ur3.forward_Kine(ur3._result[i], res)){
            std::cout << i << " " << "res:" << std::endl;
            std::cout << res << std::endl;
        }
    }

    return 0;
}

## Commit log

2023-10-16 initial repo
    [stlink.cfg]
2023-11-08 Add some necessary files that can control the robotic arm perfectly
    [001小圆盘+舵盘Z.SLDPRT, 002小圆盘+支架.SLDASM, 003 云台.SLDASM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]
2023-12-18 Fix bugs, add more functions, upload more videos to introduce the prj
    [kinetic.cpp, kinetic.h]

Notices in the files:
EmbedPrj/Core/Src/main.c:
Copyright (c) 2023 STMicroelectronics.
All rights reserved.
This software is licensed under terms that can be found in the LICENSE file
